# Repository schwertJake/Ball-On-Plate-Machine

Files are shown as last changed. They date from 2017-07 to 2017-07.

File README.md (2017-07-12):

# 3 DOF Arduino/Python Ball-on-plate System

# General Overview
This goal of this project is to effectively control a weighted ball on a flat surface.
Control is accomplished by the following mechanisms:
- A resistive 4 wire touchscreen is used to find ball position
- 3 Servo motors are positioned in an equilateral triangle for tilting the plate
- An Arduino Due is used to perform calculations - reading the touchscreen and moving the servos
- A python/kivy frontend is used for end user control

The entire project is built around using a PID method to properly move the ball to the setpoint.
For those not familiar, a PID control loop equation looks like the following:



Where e is the error and Kp, Ki, and Kd are all user defined constants.

For the purpose of this project, error will be calculated as the distance from the ball to the line perpendicular to
each particular servo's line of action centered around the setpoint.

The use of this PID control system allows for some interesting functionality:

- Keeping Ball Centered:


- Moving the ball among "corners":


- Moving the ball in a circle:



And more! You're basically limited to your imagination, as the base algorithm allows for changing the setpoint during runtime (and many more tuning options).

# Mechanical Components
The machine operates mechanically with the following components:

- A triangular bracket to securely mount the touch screen
- 3 'fork' arms with rod ends on all sides to translate servo movements to plate tilt
- 3 Aluminum servo mounts to securely mount the servos
  - These include ball bearings and a pinion attachment to allow for purely rotational movement
- A circular base for the servo mounts to attach to
- 3 circular feet to elevate the base

This design allows for a full range of motion by all servo arms without any binding regardless or the other 2 servos.

All components were designed in Solidworks and 3D printed other than the servo mounts and some misc. hardware. Find all STL files needed to build this system in the STL_Files folder.

# Electrical Components
The machine utilizes the following electrical components:

- A 5V/4A power supply delivers power from the wall to the 3 servos
- The Arduino Due microcontroller uses a micro-USB connection for both power and serial communication
- Each servo runs off of 5V power, and is position controlled by a PWM pin on the Due
- The resistive touchscreen uses 4 wires read by analog ports of the Due to determine ball position
- A serial 0.1uF capacitor (to ground) is added to each touchscreen wire to help filter input

# Arduino Software 
The Arduino Due does the majority of calculations and directly controls all components.

Here's a top level look at the arduino side control flow:



There are too many small implementation details to go over in the readme, but some highlights are:
- Touchscreen reading is done using a running median filter
- Functionality for changing PID parameters during runtime is built in but not used
- 2nd derivative damping functionality is added but also not used

The basis of the program is performing PID calculations for a given ball position and setpoint 
(which can and will be moved around during runtime). All other features are built around the core
PID method.

The computation time (amount of elapsed time between running PID calculations) can be changed at compile time,
but was found to be most stable at ~10ms

# Python/Kivy Front End
To make the machine more user friendly, a python front end was built on top of Kivy framework to show analytics and control the operations.

Features include:

- Real time graphing or each servo's error measurements (remember, PID output is calculated individually per servo as they all have different lines of action!)





- PID value sliders - allowing adjustment and tuning of the algorithm during run time
- Various buttons to control the operation of the machine (circle, center, corners, as well as some platform only demo functionality)
- Real time position graphing - both of the ball's actual position as well as the setpoint (if it is moving)



Of course all the other wonderful benefits that come with the Kivy framework are baked in - including touchscreen optimization, size scalability, and cross platform usage.

# What's Next?

This project has come a long way, but there is still plenty of functionality left to add!
Some of the things I'm interested in adding are:
- Joystick functionality: Control where the ball moves with an analog joy stick!
- PCB/Enclosure: I've been sitting on a PCB design that will simplify the rats nest. With the addition of a PCB, building a full enclosure for the machine will be much easier
- Computer Vision: Essentially the revision 2 of the project - use the same PID control algorithm but use a top mounted webcam with openCV for input instead of the resistive touchscreen. This allows for a more versatile selection of balls, as the touchscreen is limited to especially heavy ball bearings

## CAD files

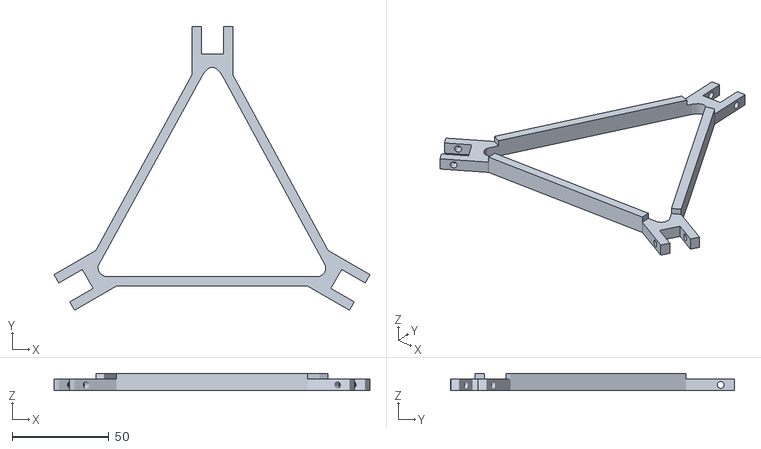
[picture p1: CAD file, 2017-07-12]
STL_Files/PIDTop.STL
163.7 x 146.9 x 9.00

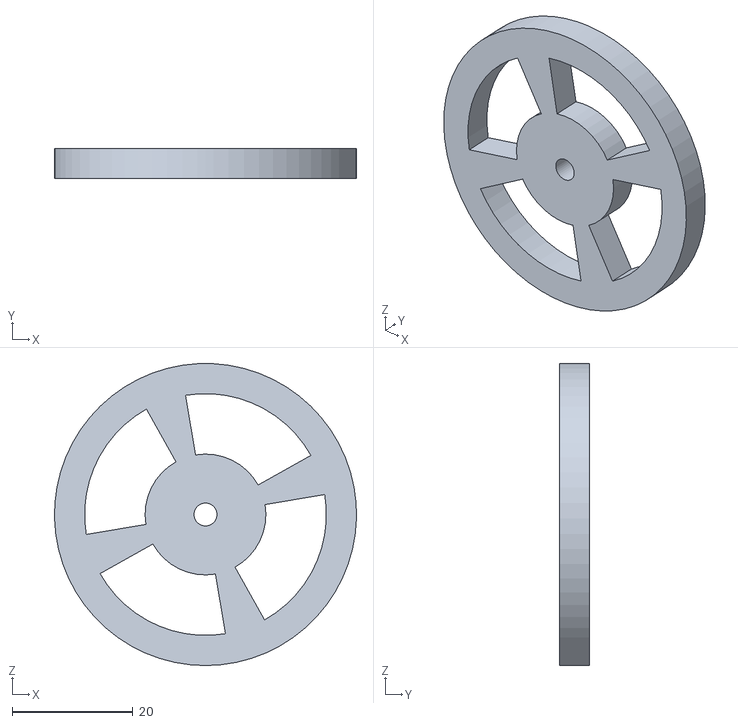
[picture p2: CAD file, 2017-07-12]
STL_Files/PIDfoot.STL
50.0 x 5.00 x 50.0

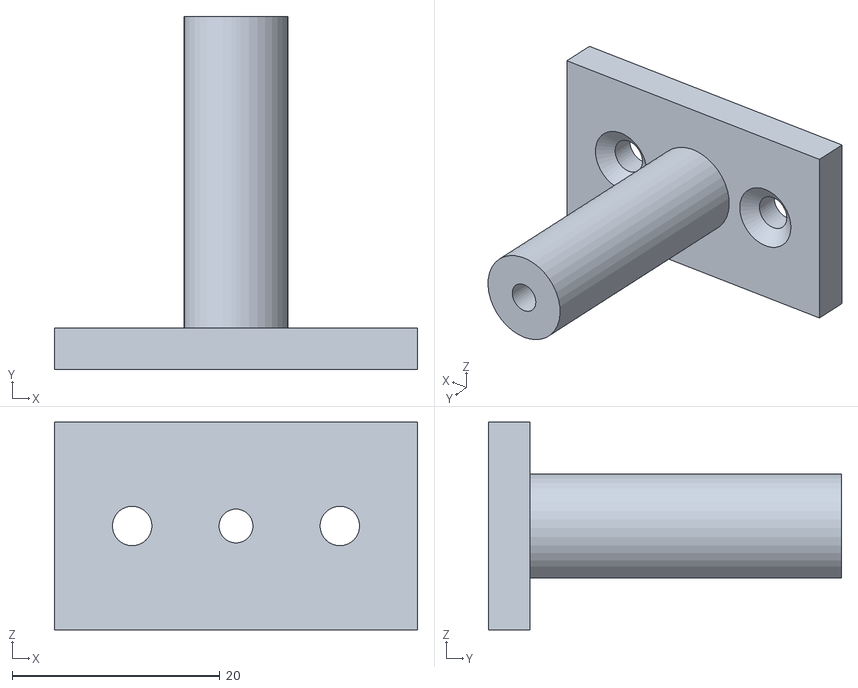
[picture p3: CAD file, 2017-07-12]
STL_Files/PIDleg.STL
35.0 x 34.0 x 20.0

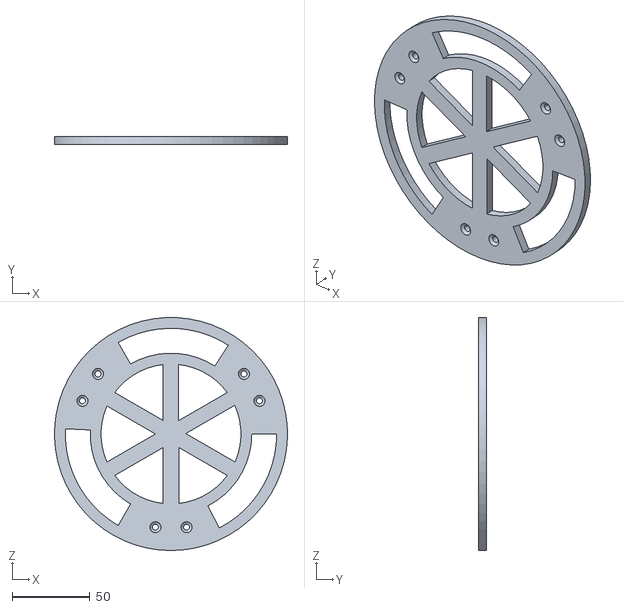
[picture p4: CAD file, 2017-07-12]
STL_Files/PIDBase.STL
150.0 x 5.00 x 150.0

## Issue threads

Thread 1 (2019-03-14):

AttributeError: 'super' object has no attribute '__getattr__'

mentablack, 2019-03-14:
While running pid.py  it gives me an error

File "C:\Users\Desktop\Python Program\kivya.py", line 50, in __init__
     self.ids.graph_1.add_plot(self.plot)
   File "kivy\properties.pyx", line 841, in kivy.properties.ObservableDict.__getattr__
 AttributeError: 'super' object has no attribute '__getattr__'

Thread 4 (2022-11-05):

error on serial

FrankdeJesus, 2022-11-05:
hi everyone

I get all the time this error when i launch begin com

Exception in thread Thread-1 (get_serial):
 Traceback (most recent call last):
   File "C:\Program Files\Python310\lib\threading.py", line 1016, in _bootstrap_inner
     self.run()
   File "C:\Program Files\Python310\lib\threading.py", line 953, in run
     self._target(*self._args, **self._kwargs)
   File "C:\Users\Armand_Novalys\Desktop\Projet_Fin_Etude (PFE)\Arduino\PROJET\3DOF_(2)\PID_Arduino_DUE\pid.py", line 182, in get_serial
     new_info = self.ser.readline().decode('utf-8')[:-2].split(',')
 UnicodeDecodeError: 'utf-8' codec can't decode byte 0x96 in position 1: invalid start byte

and when i click o, circle or square and center it also sends

serial not found

i use arduino mega board and i also change the wode where it need to be change like serial.USB and analogresolution

kiss hope you answer my issue

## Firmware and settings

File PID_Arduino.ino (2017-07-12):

// -------------------- Import Libraries --------------------
#include <Servo.h>
#include <inttypes.h>
#include <stdlib.h>
// -------------------- End Libraries --------------------


// -------------------- Running Median Class --------------------
template <typename T, uint8_t N, T default_value> class FastRunningMedian 
{
  public:
    // ---------- Constructor ----------
    FastRunningMedian() 
    {
      _buffer_ptr = N;
      _window_size = N;
      _median_ptr = N/2;
  
      // Init buffers
      uint8_t i = _window_size;
      while( i > 0 ) {
        i--;
        _inbuffer[i] = default_value;
        _sortbuffer[i] = default_value;
      }
    };
    // ---------- End Constructor ----------

    // ---------- Get Median ----------
    T getMedian() { return _sortbuffer[_median_ptr];}
    // ---------- End Get Median ----------

    // ---------- Add Value ----------
    void addValue(T new_value) 
    {
      if (_buffer_ptr == 0)
        _buffer_ptr = _window_size;
      
      _buffer_ptr--;
      
      T old_value = _inbuffer[_buffer_ptr]; // retrieve the old value to be replaced
      if (new_value == old_value)       // if the value is unchanged, do nothing
        return;
      
      _inbuffer[_buffer_ptr] = new_value;  // fill the new value in the cyclic buffer
        
      uint8_t i = _window_size;
      while(i > 0) 
      {
        i--;
        if (old_value == _sortbuffer[i])
          break;
      }
      
      _sortbuffer[i] = new_value; // replace the value 
  
      if (new_value > old_value) 
      {
        for(uint8_t p=i, q=i+1; q < _window_size; p++, q++) 
        {
          if (_sortbuffer[p] > _sortbuffer[q]) 
          {
            T tmp = _sortbuffer[p];
            _sortbuffer[p] = _sortbuffer[q];
            _sortbuffer[q] = tmp;
          } 
          else return;
        }
      } 
      else 
      {
        for(int p=i-1, q=i; q > 0; p--, q--) 
        {
          if (_sortbuffer[p] > _sortbuffer[q]) 
          {
            T tmp = _sortbuffer[p];
            _sortbuffer[p] = _sortbuffer[q];
            _sortbuffer[q] = tmp;
          } 
          else return;
        }
      }
    }
    // ---------- End Add Value ----------
  
  private:
    uint8_t _buffer_ptr;
    uint8_t _window_size;
    uint8_t _median_ptr;
    T _inbuffer[N];
    T _sortbuffer[N];
};
// -------------------- End Running Median Class --------------------



// -------------------- Objects --------------------
Servo servo1; //servo on y axis
Servo servo2; // lower right servo
Servo servo3; // lower left servo
FastRunningMedian<unsigned int,100, 0> xValMedian;
FastRunningMedian<unsigned int,100, 0> yValMedian;
// -------------------- End Objects --------------------



// -------------------- Constants --------------------
// -- Working Constants: --
#define outMin -400//-200
#define outMax 600//400
#define r3 1.73205 // square root of 3

// -- Touchscreen Pins: --
#define x_5v A1
#define x_gnd A2
#define y_5v A5
#define y_gnd A4

// -- Servo Pins: --
#define servopin1 9
#define servopin2 10
#define servopin3 11
// -------------------- End Constants --------------------



// -------------------- Variables --------------------
// -- Position Vars: --
double xO, yO; //setpoint
double xCor, yCor; //read from touchscreen
double xI, yI; //actual (median filtered)
double lastXI = 0, lastYI = 0;

// -- Error Vars: --
double error[3];//holds current errror
double lastError[3] = {0,0,0};
double lastLastError[3] = {0,0,0};

// ----- Output Vars: -----
double output[3]; //Hold actual output

// -- Computations Vars: --
double ITerm[3] = {0,0,0};
double lastDVal[3] = {0,0,0};
double lastLastDVal[3] = {0,0,0};
unsigned long now, deltaT, lastT;

// -- Tunings Vars: --
double setkp[3] = {0.3,0.5,0.5};
double setki[3] = {0.1,0.15,0.15};
double setkd[3] = {0.1,0.14,0.14};
double setka[3] = {1,1,1};
double aggkp[3] = {0.7,0.9,0.9};
double aggki[3] = {0.02,0.02,0.02};
double aggkd[3] = {0.1,0.1,0.1};
double aggka[3] = {0,0,0};
double kp[3], ki[3], kd[3], ka[3]; // working tunings
int compT; //computation time in ms

// -- Control Vars: --
bool aggTuningSet = false, compute_bool = true, 
  computeDone = true, setpointChange = false;
char controlByte = '1';
int servo1Rotate, servo2Rotate, servo3Rotate;
int auxTimeCount = 0, methodCount = 0;
int squareCoor[4][2] = {{1000,700}, {1000,300}, {500,300}, {500,700}};
int circleCoor[73][2] = {{950,500}, {949,517}, {947,535},
                        {943,552}, {938,568}, {931,584}, {923,600}, {914,615},
                        {903,629}, {891,641}, {879,653}, {865,664}, {850,673},
                        {835,681}, {819,688}, {802,693}, {785,697}, {768,699},
                        {750,700}, {733,699}, {715,697}, {698,693}, {666,681},
                        {650,673}, {635,664}, {622,653}, {609,642}, {597,629},
                        {586,615}, {577,600}, {569,585}, {562,569}, {557,552},
                        {553,535}, {551,518}, {550,500}, {551,483}, {553,466},
                        {557,449}, {562,432}, {569,416}, {577,400}, {586,386}, 
                        {597,372}, {608,359}, {621,347}, {635,336}, {650,327}, 
                        {665,319}, {681,312}, {698,307}, {715,303}, {732,301},
                        {750,300}, {767,301}, {784,303}, {801,307}, {818,312},
                        {834,319}, {850,327}, {864,336}, {878,346}, {891,358},
                        {903,371}, {913,385}, {923,399}, {931,415}, {938,431},
                        {943,448}, {947,465}, {949,482}, {950,499}, {949,517}};          
// -------------------- End Variables --------------------



// -------------------- Begin Setup --------------------
void setup()
{
  Serial.begin(115200); //Begin serial communications
  analogReadResolution(12); // Read touch screen using Due's 12bit ADC
  
  // ---------- Servos ----------
  // attach servo to pwn pins:
  servo1.attach(servopin1);
  servo2.attach(servopin2);
  servo3.attach(servopin3);
  // level the servos:
  servo1.write(1500);
  servo2.write(1500);
  servo3.write(1500);
  // ---------- End Servos ----------
  
  // ---------- PID Init ----------
  //  These values can be initially set or set in real time
  xO =750;
  yO = 500;
  compT = 10;
  setPIDTunings(false);
  // ---------- End PID Init ----------
}
// -------------------- End Setup --------------------



// -------------------- Begin Main Loop --------------------
void loop()
{
  readTouchData();

  // if control byte calls for PID calculations, do so:
  if(compute_bool)
  {
    if(controlPID())
    {
      writeServos();
      computeDone = true;
    }
  }
  
  // This block runs once per compT, after PID is calculated:
  if(computeDone)
  {
    sendCoordinates();
    recieveSerial();

    switch(controlByte)
    {
      case('1'): // Setpoints make a square
        auxTimeCount++;
        if(auxTimeCount > 100)
        {
          corners(); // changes setpoint
          auxTimeCount = 0;
          setpointChange = true;
        }
        else setpointChange = false;
        break;
    
      case('2'): // Setpoints make a circle
        auxTimeCount++;
        if(auxTimeCount > 2)
        {
          circle(); //changes setpoint
          auxTimeCount = 0;
          setpointChange = true;
        }
        else setpointChange = false;
        break;
    
      case('5'):
        rotate();
        break;
    
      default:
        break;
    }    
    computeDone = false;
  }
}
// -------------------- End Main Loop --------------------



// -------------------- PID Methods --------------------
// ---------- Control PID ----------
// Main control function that calls and controls
// PID algorithm, returns true if PID was recalculated
bool controlPID()
{
  // check the elapsed time since last compute:
  now = millis(); // current time
  deltaT = now - lastT; // last compute time
  
  if(deltaT >= compT) // if compT time has elapsed
  { 
    for(int i=0; i<3; i++) // for each servo
    { 
      readTouchData(); // continue checking touchscreen
      getCoordinates(); // get coordinate from median filter
      readTouchData();
      getError(i); // finds error values
      readTouchData();
      computePID(i); // computes output from PID algorithm
      readTouchData();
      limitOutput(i); // limit the output
    }
    lastT = now; //keep track of last compute time    
    return true; //PID was calculated
  }
  else return false; //PID wasn't calculated
}
// ---------- End Control PID ----------

// ---------- Compute PID ----------
// PID algorithm that calculates the output
// for each servo
void computePID(int i)
{

  // to mitigate touchscreen errors, make sure current
  // error is within 10 of last error. If not, ignore it.
  if(controlByte == '0' || setpointChange)
    if(abs(error[i] - lastError[i]) > 10) error[i] = lastError[i];
  
  // calculate each PID term individually:
  double PTerm = error[i] * kp[i];
  ITerm[i] += (ki[i] * error[i]);
  double DVal = (error[i] - lastError[i]);
  double DTerm = kd[i] * (((5*DVal) + (3*lastDVal[i]) + (2*lastLastDVal[i]))/10.0);
  double ATerm = ka[i] * (((DVal - lastDVal[i]) + (lastDVal[i] - lastLastDVal[i]))/2.0);
      
  // Calculate Output:
  output[i] = PTerm + ITerm[i] + DTerm + ATerm;

  // save some calculations for later:
  lastError[i] = error[i];
  lastLastDVal[i] = lastDVal[i];
  lastDVal[i] = DVal;
}
// ---------- End Compute PID ----------

// ---------- Limit Output ----------
// Limits output from Compute PID to keep
// servo output within user defined bounds
void limitOutput(int i)
{
  if(output[i] > outMax) output[i] = outMax;
  else if(output[i] < outMin) output[i] = outMin;
  if(ITerm[i] > outMax) ITerm[i] = outMax;
  else if(ITerm[i] < outMin) ITerm[i] = outMin;
}
// ---------- End Limit Output ----------

// ---------- Get Error ----------
//  Computes the difference in the current
//  position and the perpendicular line of
//  action for each servo
void getError(int i)
{
  if (i == 0) // for servo1: (on y axis)
    error[0] = (yI - yO);

  if (i == 1) // for servo2 (120deg CW from servo1)
    error[1] = (r3*(xI - xO) + (yO-yI))/2.0;

  if (i == 2) // for servo3 (120deg CCW from servo1)
    error[2] = (r3*(xO - xI) + (yO-yI))/2.0;
}
// ---------- End Get Error ----------

// ---------- Set PID Parameters ----------
//  Because compute time is variable, this
//  method normalizes PID tunings against time
//  You can also select aggressive or standard tunings
//  by passing in a boolean variable (true = aggressive)
void setPIDTunings(bool aggressive)
{
  if(!aggressive)
    for(int i = 0; i < 3; i++)
    {
      kp[i] = setkp[i];
      kd[i] = setkd[i] / (compT/1000.0);
      ki[i] = setki[i] * (compT/1000.0);
      ka[i] = setka[i] * (compT/1000.0);
    }
  else
    for(int i = 0; i < 3; i++)
    {
      kp[i] = setkp[i];
      kd[i] = setkd[i] / (compT/1000.0);
      ki[i] = setki[i] * (compT/1000.0);
      ka[i] = setka[i] * (compT/1000.0);
    }
}
// ---------- End Set Parameters ----------

// ---------- Write Servos ----------
// This method sends the PID output to the Servos
void writeServos()
{
  servo1.write(1610 - output[0]);
  servo2.write(1610 + output[1]);
  servo3.write(1590 + output[2]);
}
// ---------- End Write Servos ----------
// -------------------- End PID Methods --------------------



// -------------------- Touchscreen Methods --------------------
// ---------- Read Touch Data ----------
//  Reads the position from the 4 wire touchscreen
//  and maps it to a 1500x1000 coordinate system
void readTouchData()
{
  //read x-position
  pinMode(x_5v,  OUTPUT);
  pinMode(x_gnd,  OUTPUT);
  pinMode(y_5v,  INPUT);
  pinMode(y_gnd,  INPUT);
  digitalWrite(x_5v, HIGH);
  digitalWrite(x_gnd, LOW);
  xCor = map(analogRead(y_5v), 400, 3600, 1500, 0 );
    
  //read y-position
  pinMode(x_5v,  INPUT);
  pinMode(x_gnd,  INPUT);
  pinMode(y_5v,  OUTPUT);
  pinMode(y_gnd,  OUTPUT);
  digitalWrite(y_5v, HIGH);
  digitalWrite(y_gnd, LOW);
  yCor = map(analogRead(x_5v), 700, 3300, 0, 1000);

  xValMedian.addValue(xCor);
  yValMedian.addValue(yCor);
}
// ---------- End Read Touch Data ----------

// ---------- Get Coordinates ----------
// gets coordinate value from median filter
void getCoordinates()
{
  xI = xValMedian.getMedian();
  yI = yValMedian.getMedian();
}
// ---------- End Get Coordinates ----------
// -------------------- End Touchscreen Methods --------------------



// -------------------- Auxilary Methods --------------------
// ---------- Send Coordinates ----------
// Sends errors, setpoint, and actual position
// to the python frontend to be displayed
void sendCoordinates()
{
  SerialUSB.print(error[0]);
  SerialUSB.print(",");
  SerialUSB.print(error[1]);
  SerialUSB.print(",");
  SerialUSB.print(error[2]);
  SerialUSB.print(",");
  SerialUSB.print(xO);
  SerialUSB.print(",");
  SerialUSB.print(yO);
  SerialUSB.print(",");
  SerialUSB.print(xI);
  SerialUSB.print(",");
  SerialUSB.println(yI);
}
// ---------- End Send Coordinates ----------

// ---------- Recieve Serial ----------
//  For the front end to communicate with
//  the machine, instructional bytes will
//  be sent and recieved with this message
bool recieveSerial()
{
  if(Serial.available() > 0)
  {
    int incomingByte = Serial.read();
    controlByte = (char)incomingByte;
    Serial.println(controlByte);
    switchOnce();
    return true;
  }
  else return false;
}
// ---------- End Recieve Serial ----------

// ---------- Tuning Switch ----------
//  If there was a new instruction recieved
//  from the front end, change actions
void switchOnce()
{
  int tempVar = 0;
  switch(controlByte)
  {
    case('P'): // change setkp
      tempVar = Serial.read();
      setkp[0] = (tempVar - 48)*0.1;
      setkp[1] = (tempVar - 48)*0.1;
      setkp[2] = (tempVar - 48)*0.1;
      controlByte = '0';
      xO = 750;
      yO = 500;
      setPIDTunings(true);
      compute_bool = true;
      break;
    
    case('I'): // change setki
      tempVar = Serial.read();
      setki[0] = (tempVar - 48)*0.01;
      setki[1] = (tempVar - 48)*0.01;
      setki[2] = (tempVar - 48)*0.01;
      controlByte = '0';
      xO = 750;
      yO = 500;
      setPIDTunings(true);
      compute_bool = true;
      break;
    
    case('D'): //change setkd
      tempVar = Serial.read();
      setkd[0] = (tempVar - 45)*0.01;
      setkd[1] = (tempVar - 43)*0.01;
      setkd[2] = (tempVar - 43)*0.01;
      controlByte = '0';
      xO = 750;
      yO = 500;
      setPIDTunings(true);
      compute_bool = true;
      break;
    
    case('0'): // centers ball
      xO = 750;
      yI = 500;   
    case('1'): // makes ball go in a square
    case('2'): // makes ball go in circles
      compute_bool = true;
      break;
    
    case('5'): // rotates platform
      compute_bool = false;
      servo1Rotate = 1500;
      servo2Rotate = 1900;
      servo3Rotate = 1100;
      break;
    
    case('3'): // raises the platform
      servo1.write(1100);
      servo2.write(1900);
      servo3.write(1900);
      compute_bool = false;
      break;
    
    case('4'): // lowers the platform
      servo1.write(1900);
      servo2.write(1100);
      servo3.write(1100);
      compute_bool = false;
      break;
    
    default:
      break;
  }
}
// ---------- End Tuning Switch ----------

// ---------- Corners ----------
// setpoint moves through the 4 corners
// on the screen, making the ball travel
// in a square
void corners()
{
  xO = squareCoor[methodCount][0];
  yO = squareCoor[methodCount][1];
  methodCount++;
  if(methodCount > 3) methodCount = 0;
}
// ---------- End Corners ----------

// ---------- Circle ----------
// setpoint moves in a circle around
// the center of the screen
void circle()
{
  xO = circleCoor[methodCount][0];
  yO = circleCoor[methodCount][1];
  methodCount++;
  if(methodCount > 72) methodCount = 0;
}
// ---------- End Circle ----------

// ---------- Rotate ----------
// Rotates the platform through its (mostly)
// full range of motion as a demo
void rotate()
{
  servo1Rotate--;
  if(servo1Rotate < 1100) servo1Rotate = 1900;

  servo2Rotate++;
  if(servo1Rotate > 1900) servo2Rotate = 1100;

  servo3Rotate++;
  if(servo3Rotate > 1900) servo3Rotate = 1100;

  servo1.write(servo1Rotate);
  servo2.write(servo2Rotate);
  servo3.write(servo3Rotate);
}
// ---------- End Rotate ----------
// -------------------- End Auxilary Methods --------------------

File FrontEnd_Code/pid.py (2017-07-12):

from kivy.app import App
from kivy.uix.floatlayout import FloatLayout
from kivy.properties import StringProperty
from kivy.clock import Clock
from threading import Thread
import serial
from queue import Queue
from kivy.garden.graph import MeshLinePlot
from kivy.core.window import Window
from kivy.config import Config

class pid(FloatLayout):
    # ----- Real Time Plotting List -----
    plot_1_list = []
    plot_2_list = []
    plot_3_list = []
    setpoint_list = []
    actual_list = []

    # ----- System Control Variables -----
    lit_button = None
    coms_on = False
    serial_read = False

    # ----- Tuning Variables -----
    p_val = 3.5
    i_val = 0
    d_val = 9

    # ---------- Init ----------
    # Initialize Kivy window, setup realtime
    # graphs, schedule update intervals, and
    # initialize the queue
    def __init__(self):
        super(pid, self).__init__()
        Window.clearcolor = (.14, .18, .2, 1)

        # Initialize but don't open serial coms
        self.ser = serial.Serial()
        self.ser.port = 'COM8'

        # Create Mesh Line Plots
        self.plot = MeshLinePlot()
        self.plot2 = MeshLinePlot()
        self.plot3 = MeshLinePlot()
        self.setpoint_plot = MeshLinePlot()
        self.act_pos_plot = MeshLinePlot()

        # Add line plots to graph
        self.ids.graph_1.add_plot(self.plot)
        self.ids.graph_2.add_plot(self.plot2)
        self.ids.graph_3.add_plot(self.plot3)
        self.ids.pos_graph.add_plot(self.setpoint_plot)
        self.ids.pos_graph.add_plot(self.act_pos_plot)

        # Assign colors to line plots
        self.plot.color = [0, 1, 0, 1]
        self.plot2.color = [1,0,0,1]
        self.plot3.color = [0,0,1,1]
        self.setpoint_plot.color = [0,1,0,1]
        self.act_pos_plot.color = [1,0,0,1]

        # Schedule Intervals
        self.graph_clock = Clock.schedule_interval(self.get_plot_points, (1/10))
        self.graph_clock.cancel()
        self.slider_clock = Clock.schedule_interval(self.pid_listener, (1 / 30))

        # initialize a que to store incoming serial coms
        self.q = Queue()
    # ---------- End Init ----------


    # ---------- PID Listener ----------
    # Checks to see if slider PID values have changed
    # If they have, send new value via serial
    def pid_listener(self, other):
        # Check P Value:
        if(self.p_val != float(self.ids.p_slider.value)):
            self.send_serial((",".join(["p", str(self.ids.p_slider.value)])), "")
            self.p_val = self.ids.p_slider.value

        # Check I Value:
        if(self.i_val != float(self.ids.i_slider.value)):
            self.send_serial((",".join(["i", str(self.ids.i_slider.value)])), "")
            self.i_val = self.ids.i_slider.value

        # Check D Value:
        if(self.d_val != float(self.ids.d_slider.value)):
            self.send_serial((",".join(["d", str(self.ids.d_slider.value)])), "")
            self.d_val = self.ids.d_slider.value
    # ---------- End PID Listener ----------


    # ---------- Coms Btn Press ----------
    # Turns serial communication on/off
    # also changes coms button color/text
    def coms_btn_press(self):
        # If coms are being turned off:
        if self.coms_on:
            self.coms_on = False
            self.ids.coms_btn.background_color = [1,.73,0,1]
            self.graph_clock.cancel()
            self.ids.coms_btn.text = "Begin Coms"
            self.serial_read = False
        # If coms are being turned on:
        else:
            self.coms_on = True
            self.ids.coms_btn.background_color = [0,.8,.42,1]
            self.graph_clock()
            self.ids.coms_btn.text = "End Coms"
            self.serial_read = True
            get_serial_thread = Thread(target=self.get_serial)
            get_serial_thread.daemon = True
            get_serial_thread.start()
    # ---------- Coms Btn Press ----------


    # ---------- Reset All ----------
    # Resets to starter PID parameters
    # and centers values
    def reset_all(self):
        # Reset Slider Values:
        self.ids.p_slider.value = 3.5
        self.ids.i_slider.value = 0
        self.ids.d_slider.value = 9

        # Pull ball to the center:
        self.send_serial(0, "PASS")
    # ---------- End Reset All ----------


    # ---------- Get Plot Points ----------
    # Clock scheduled method that checks queue
    # for new data points, and adds it to the
    # real time graphs
    def get_plot_points(self, other):
        # Reset error plots every 2000 data points
        if (len(self.plot_1_list) > 2000):
            self.plot_1_list = []
            self.plot_2_list = []
            self.plot_3_list = []

        # Reset position plots every 1000 data points
        if (len(self.actual_list)) > 1000:
            self.actual_list = []
            self.setpoint_list = []

        # If the queue has data, append it to the plot lists
        while not self.q.empty():
            temp_vals = self.q.get()
            self.plot_1_list.append(float(temp_vals[0]))
            self.plot_2_list.append(float(temp_vals[1]))
            self.plot_3_list.append(float(temp_vals[2]))
            self.setpoint_list.append((float(temp_vals[3]),float(temp_vals[4])))
            self.actual_list.append((float(temp_vals[5]), float(temp_vals[6])))

        # Append plot lists to mesh line plots
        self.plot.points = [(i, j) for i, j in enumerate(self.plot_1_list)]
        self.plot2.points = [(i, j) for i, j in enumerate(self.plot_2_list)]
        self.plot3.points = [(i, j) for i, j in enumerate(self.plot_3_list)]
        self.act_pos_plot.points = list(self.actual_list)
        self.setpoint_plot.points = self.setpoint_list[:]
    # ---------- End Get Plot Points ----------

    # ---------- Get Serial (Threaded) ----------
    # Grabs a line from serial comms
    # Should be a valued pair from arduino
    # Splits at comma and puts in queue
    def get_serial(self):
        try: # Try and open serial port
            if not self.ser.is_open:
                self.ser.open()

        except: # Serial Port isn't connected
            print("No Serial Found!")

        else: # If serial port is opened, start scanning for data
            while self.serial_read:
                # Data is sent as byte stream, we need to decode:
                new_info = self.ser.readline().decode('utf-8')[:-2].split(',')
                # Put new data in the queue for the GUI to display
                self.q.put(new_info)
    # ---------- End Get Serial ----------

    # ---------- Send Serial ----------
    # Sends commands over serial to change
    # machine's behaviour or tunings
    def send_serial(self, num, text, btn_id):
        try: # try to open serial and write command
            if not self.ser.is_open:
                self.ser.open()
            self.ser.write(str(num).encode('utf-8'))
            print(num, instr)
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
